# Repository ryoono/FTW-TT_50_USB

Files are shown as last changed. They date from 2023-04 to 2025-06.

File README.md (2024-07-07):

# FTW-TT_50_USB  

<span style="color: red; ">F</span>ake <span style="color: red; ">T</span>ype <span style="color: red; ">W</span>riter - <span style="color: red; ">T</span>etora <span style="color: red; ">T</span>ech lab _ <span style="color: red; ">5</span>.<span style="color: red; ">0</span>v _ <span style="color: red; ">USB</span> drive  
テトラ技研製 USB駆動 ニセタイプライター  

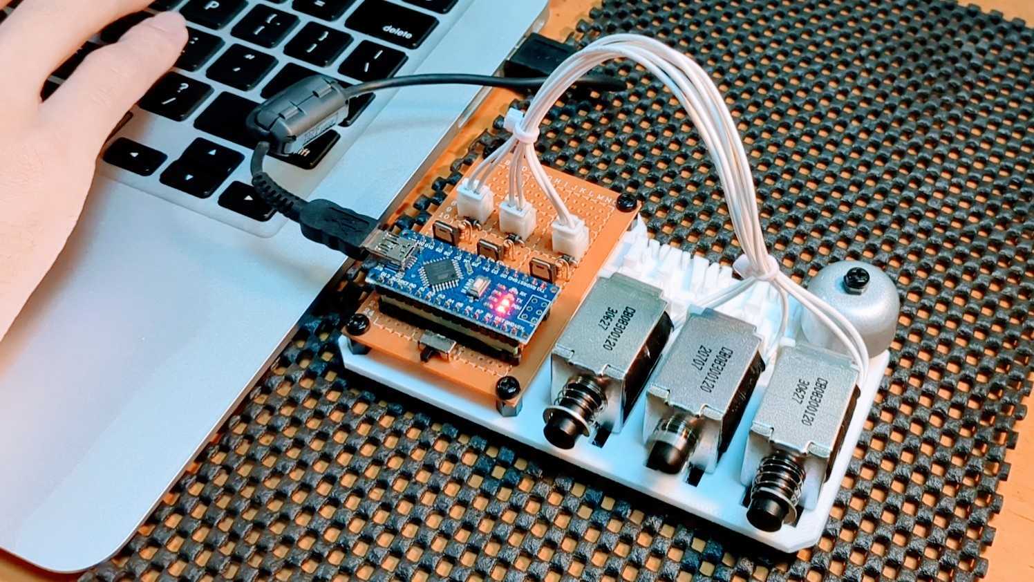
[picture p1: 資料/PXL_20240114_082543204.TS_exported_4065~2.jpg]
外観


**[紹介動画](https://youtu.be/UQrdH8_pX44?si=VVSs2FK_6RHxstvM)**

## 背景  
現代の消音キーボードに反抗すべく、タイプライターを叩いた時の音を楽しめるデバイスを作成する。  
タイプライター風キーボードも売ってはいるが、それを使っては味気ないので、外付けUSBデバイスとして実装する。  
当初、リレーで音を出そうと考えていたが、よくよく調べてみると二番煎じだった。  
そのため、急遽ソレノイドで音を出す仕様に変更した...   
[Silriumさん_USB KeyBoard RELAY](https://makezine.jp/blog/2015/08/mft2015_silrium.html)

## 概要  
キータイプ時にソレノイドを動作させ、タイプライターの音を表現する。  
音は2種類用意する。

| キー種類 | 音 | 備考 | 
| --- | --- | --- |
| 一般キー | メカニカル音 | エンターキー以外のキー | 
| エンターキー | ベル音 | |  

メカニカル音はソレノイドの動作音で再現する。  
ベル音はタイプライターの文字送り催促ベルを指しており、自転車のベルで再現する。  

## ハードウェア設計  
### 構成  
一般キー押下時の音を再現するために、ソレノイドを接続する。  
タイピングの間隔が80msを下回ると、ソレノイドのデッドタイムとかぶるため、一般キー用のソレノイドを2つ接続して対策する。  
エンターキー押下時の音は、ベルを鳴らすことで対応する。  
なお、エンターキーの押下間隔は80msを下回らないと仮定して、ソレノイドは1つのみ接続する。  
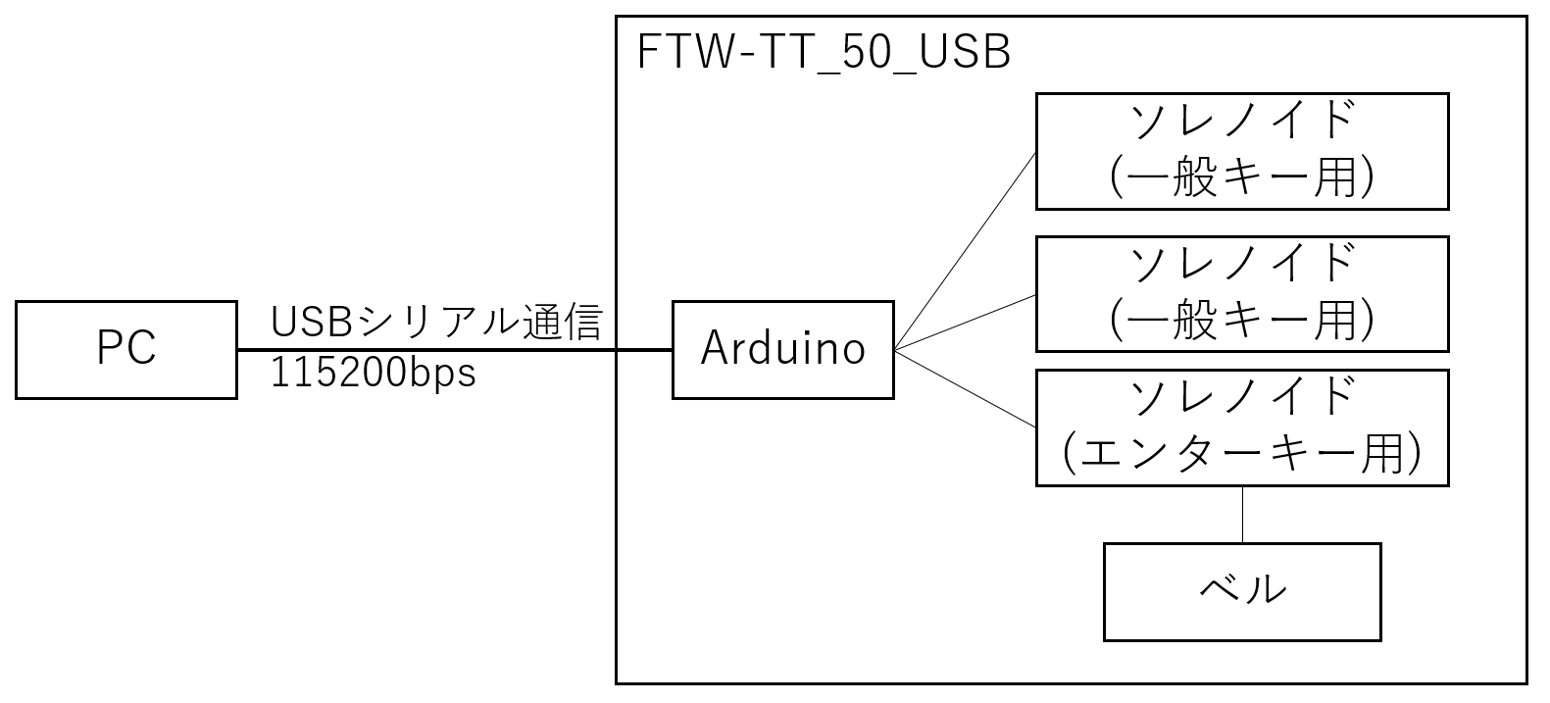
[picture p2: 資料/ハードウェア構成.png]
ハードウェア構成
 

### 回路図  
小型化を狙いpicマイコンで実装しようとしたが、時間が無いのでArduinoを使用する。  
Arduino Microを使用して設計したが、電源回りが弱いようで5Vピンから5V出力されないため、Nanoを使用する。  
使用するソレノイドには、ON/OFF 40[ms]ずつ計80[ms]のデッドタイムがあり、一般キー押下タイミングによっては、反応が追い付かない。  
そのため、ソレノイドを2個設置し、40[ms]のデッドタイムとすることで対応する。  
なお、2個以上のソレノイドを同時に動作させることはUSB2.0の規格上、電流が大きすぎるため同時動作ソレノイドは1つまでとする。  
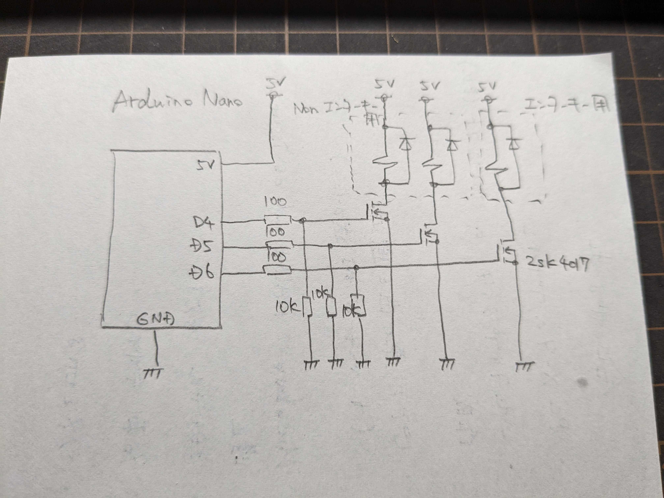
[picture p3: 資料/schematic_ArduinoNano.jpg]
schmatic
  

## ソフトウェア設計  
### PC側  
```mermaid
---
title: Fig. PC側処理_フローチャート
---

flowchart TD
    start1([開始])
    node0[Arduinoとの通信開始]
    node1[キーイベント監視開始]
    end1([終了])

    start2([キーイベント発生])
    node2[押下キー取得]
    switch1{押下キー}
    node3[Arduinoに'0'を送信]
    node4[Arduinoに'1'を送信]
    end2([終了])

    start1 --> node0
    node0 --> node1
    node1 --> end1

    start2 --> node2
    node2 --> switch1
    switch1 -- エンターキー --> node3
    switch1 -- エンターキー以外 --> node4
    node3 --> end2
    node4 --> end2
```

### デバイス側  
なぜ関数化しなかったのかが悔やまれるが、展示ギリギリだったので許してほしい。  

```mermaid
---
title: Fig. Arduino側処理_フローチャート
---

flowchart TD
    start1([開始])
    node0[シリアル受信チェック]
    switch0{受信有無}
    switch1{打鍵タイプ}
    switch2{受信キー}
    switch2_1{受信キー}
    node1[受信キーBuff = エンターキー]
    switch3{受信キーBuff}
    node2[受信キーBuff = 一般キー]
    node2_1[受信キーBuff = 一般キー]
    switch4{ソレノイド状態}
    end1([終了])

    start1 --> node0
    node0 --> switch0
    switch0 -- あり --> switch1
    switch1 -- 英語(1) --> switch2
    switch2 -- エンターキー('0') --> node1
    switch2 -- 一般キー('1') --> switch3
    switch3 -- なし(0) --> node2
    switch1 -- 日本語(0) --> switch2_1
    switch2_1 -- エンターキー('0') | 一般キー('1') --> node2_1
    node1 --> switch4
    node2 --> switch4
    switch2 -- それ以外--> switch4
    switch3 -- あり(!=0) --> switch4
    node2_1 --> switch4
    switch2_1 -- それ以外 --> switch4
    switch0 -- なし --> switch4

    switch10{受信キーBuff}
    node10[ソレノイドON時間設定 = 35ms]
    node11[ON中ソレノイドID = 3:エンターキー]
    node12[受信キーBuff初期化]

    node13[ソレノイドON時間設定 = 40ms]
    switch11{一般キーONソレノイド前回値}
    node14[ON中ソレノイドID = 1:一般キー]
    node14[ON中ソレノイドID = 2:一般キー]
    node15[受信キーBuff初期化]

    switch4 -- ON中(0以外) --> switch10
    switch10 -- エンターキー(1) --> node10
    node10 --> node11
    node11 --> node12
    switch10 -- 一般キー(0) --> node13
    node13 --> switch11
    switch11 -- 1 --> node14
    switch11 -- 2 --> node15

    switch20{ソレノイドON時間設定}
    switch21{ON中ソレノイドID}
    node20[ソレノイド1のみON]
    node21[ソレノイド2のみON]
    node22[ソレノイド3のみON]
    node23[ソレノイド全OFF]

    node30[1ms停止]

    node12 --> switch20
    node14 --> switch20
    node15 --> switch20
    switch20 -- 0以外 --> switch21
    switch21 -- 1:一般キー --> node20
    switch21 -- 2:一般キー --> node21
    switch21 -- 3:エンターキー --> node22
    switch20 -- 0 --> node23

    node20 --> node30
    node21 --> node30
    node22 --> node30
    node23 --> node30

    node30 --> end1
```

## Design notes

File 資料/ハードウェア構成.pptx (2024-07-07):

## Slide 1

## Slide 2

FTW-TT_50_USB

ソレノイド
(一般キー用)

ソレノイド
(一般キー用)

PC

USBシリアル通信
115200bps

Arduino

ソレノイド
(エンターキー用)

ベル

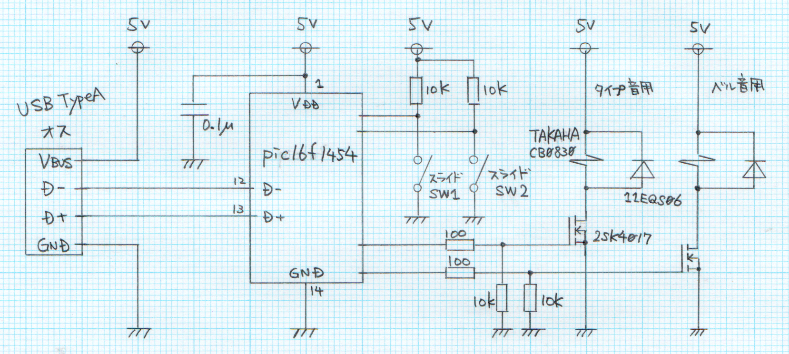
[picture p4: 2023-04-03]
資料/schematic.png

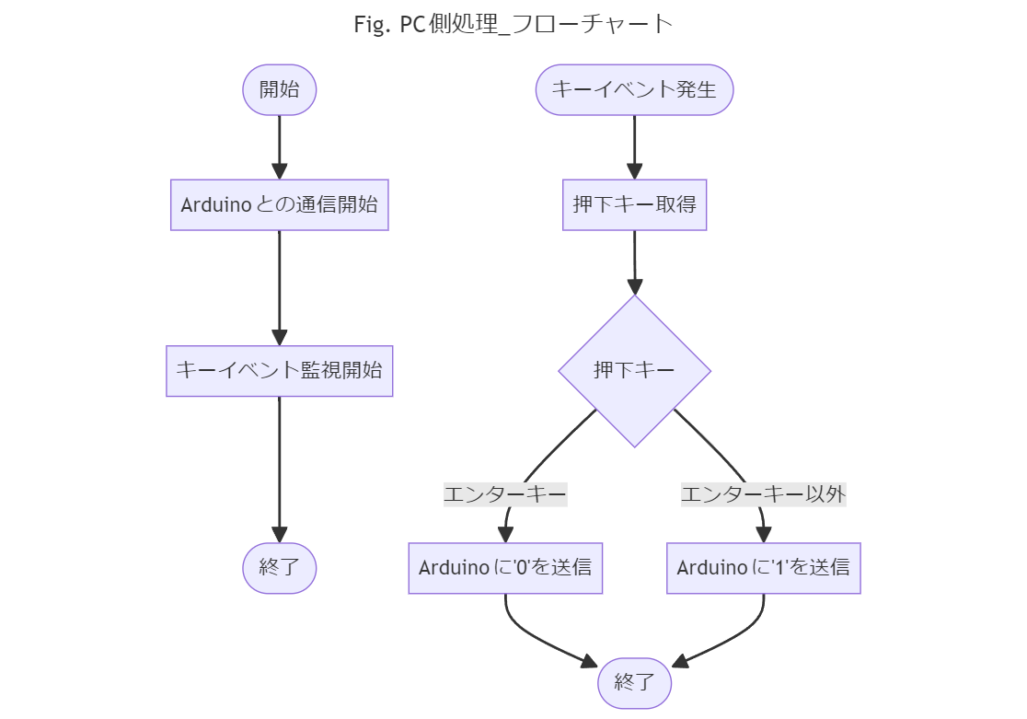
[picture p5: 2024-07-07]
資料/PC側フローチャート.png

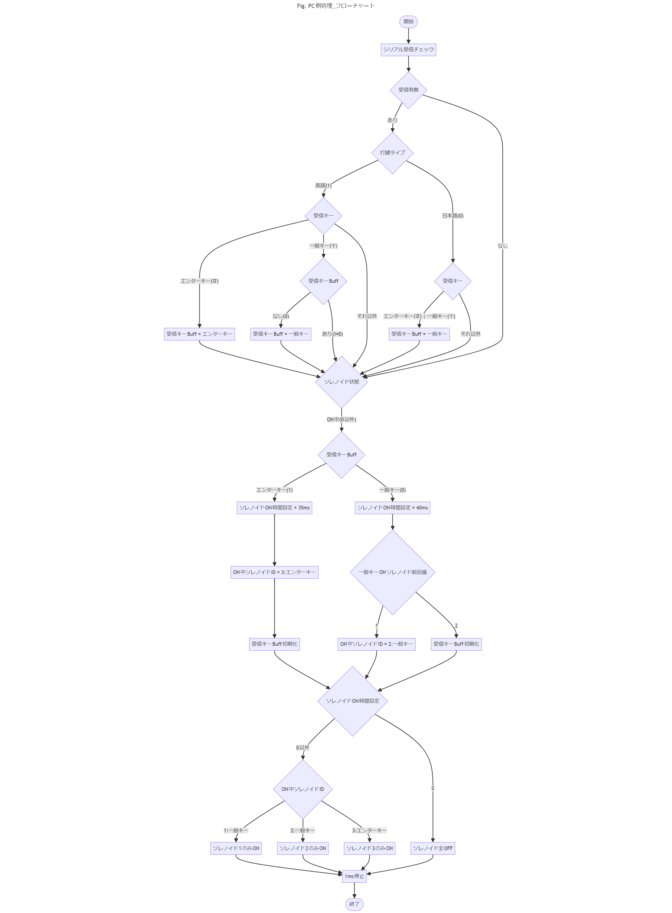
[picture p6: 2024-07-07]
資料/Arduino側フローチャート.png

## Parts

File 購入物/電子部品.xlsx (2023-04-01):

大項目 | 小項目 | 単価 | 個数 | 合計 | URL
マイコン | PIC16F1454 | 190 | 3 | 570 | https://akizukidenshi.com/catalog/g/gI-14680/
コネクタ | USBタイプA(オス) | 50 | 3 | 150 | https://akizukidenshi.com/catalog/g/gC-02236/
SW | スライドスイッチ １回路２接点 基板用 横向き | 25 | 6 | 150 | https://akizukidenshi.com/catalog/g/gP-15703/
ダイオード | ショットキーバリアダイオード ６０Ｖ１Ａ １１ＥＱＳ０６ （１０本入） | 160 | 1 | 160 | https://akizukidenshi.com/catalog/g/gI-08999/
FET | ＮｃｈパワーＭＯＳＦＥＴ ６０Ｖ５Ａ ２ＳＫ４０１７（Ｑ） | 30 | 5 | 150 | https://akizukidenshi.com/catalog/g/gI-07597/
ソケット | ＩＣソケット （１４Ｐ） （１０個入） | 100 | 1 | 100 | https://akizukidenshi.com/catalog/g/gP-00006/
基板 | 片面ガラスコンポジット・ユニバーサル基板 Ｂタイプ めっき仕上げ （９５×７２ｍｍ） 日本製 | 100 | 5 | 500 | https://akizukidenshi.com/catalog/g/gP-03230/
電解コンデンサ | 電解コンデンサー ４７μＦ１６Ｖ１０５℃ ルビコンＰＸ | 10 | 10 | 100 | https://akizukidenshi.com/catalog/g/gP-10270/
積層セラミックコンデンサ | 0.1uF | 100 | 1 | 100 | https://akizukidenshi.com/catalog/g/gP-13582/
 | 0.47uF | 110 | 1 | 110 | https://akizukidenshi.com/catalog/g/gP-15938/
抵抗 | 100Ω | 100 | 1 | 100 | https://akizukidenshi.com/catalog/g/gR-07803/
 | 15kΩ | 100 | 1 | 100 | https://akizukidenshi.com/catalog/g/gR-07840/
ソレノイド | CB0730 | 1220 | 2 | 2440 | https://www.takaha.co.jp/co/cb/
 | CB0830 | 1710 | 2 | 3420
 | CB1029 | 1830 | 2 | 3660

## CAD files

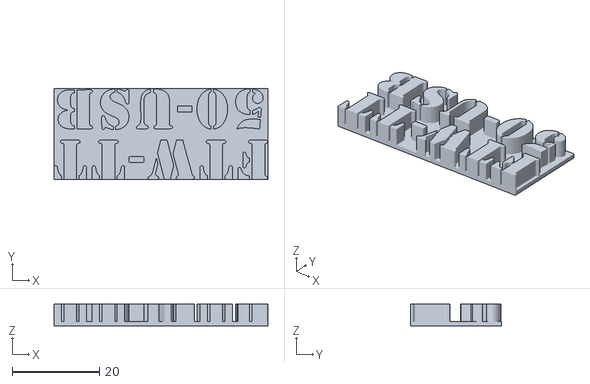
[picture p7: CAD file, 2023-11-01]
3D_Data/文字プレート.stl
49.1 x 20.8 x 5.00

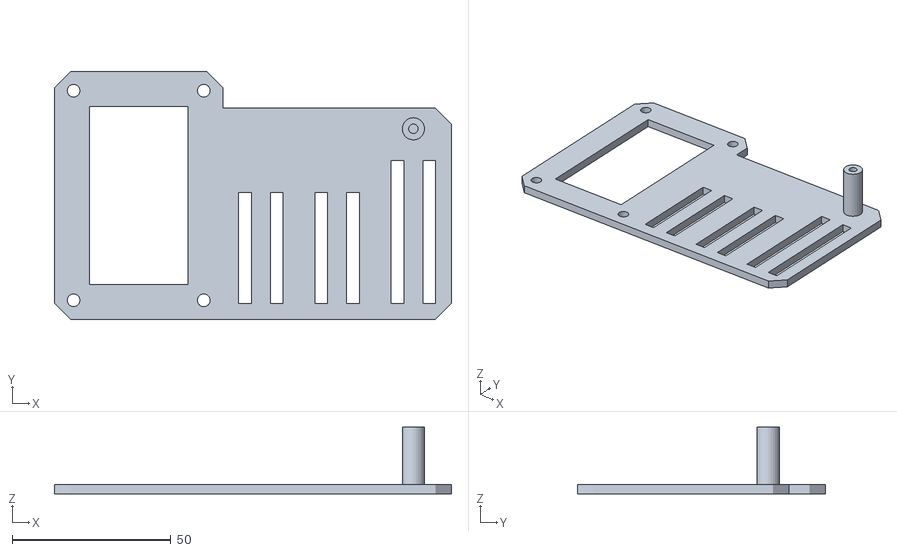
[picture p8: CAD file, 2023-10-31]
3D_Data/固定台.stl
125.0 x 78.0 x 21.0

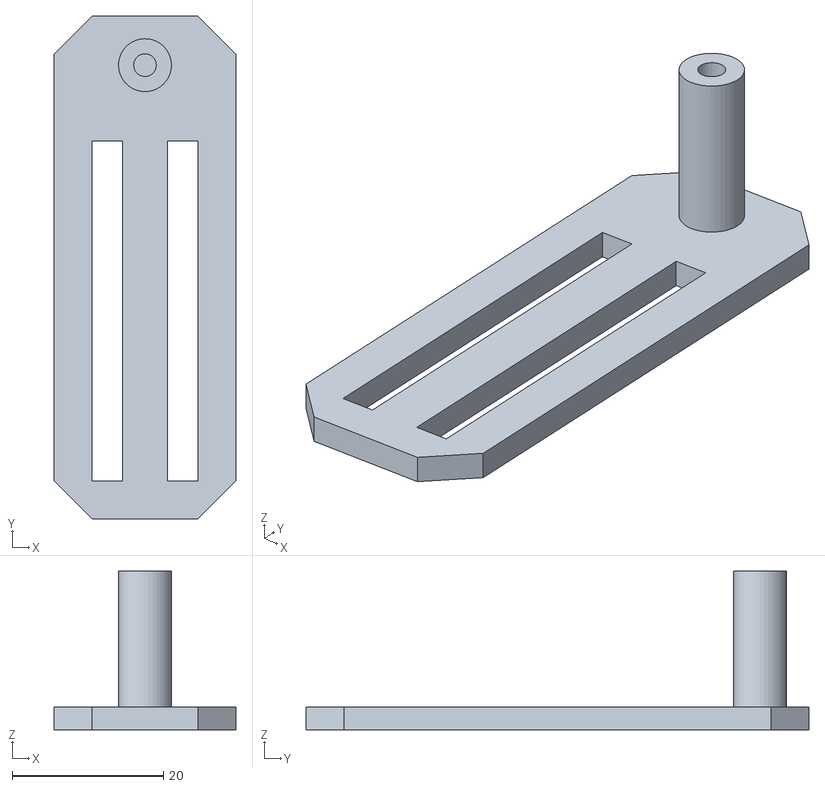
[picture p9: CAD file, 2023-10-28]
3D_Data/ベル動作確認用土台.stl
24.0 x 66.5 x 21.0

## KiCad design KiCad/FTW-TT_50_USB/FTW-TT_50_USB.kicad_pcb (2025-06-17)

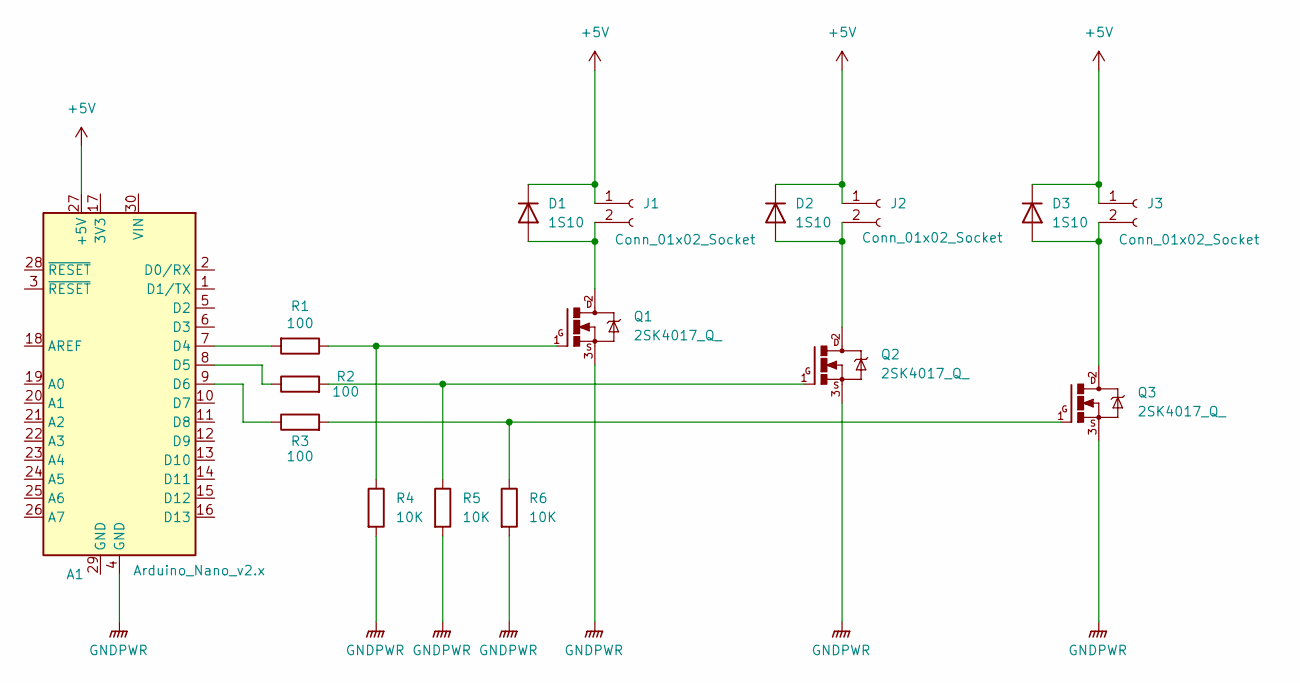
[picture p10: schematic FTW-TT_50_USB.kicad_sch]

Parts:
A1: Arduino_Nano_v2.x; Arduino_Nano
D1, D2, D3: 1S10; D_DO-41_SOD81_P7.62mm_Horizontal
J1, J2, J3: Conn_01x02_Socket; JST_XH_B2B-XH-AM_1x02_P2.50mm_Vertical
Q1, Q2, Q3: 2SK4017_Q_; TO230P230X650X740-3P
R1, R2, R3: 100; R_Axial_DIN0207_L6.3mm_D2.5mm_P10.16mm_Horizontal
R4, R5, R6: 10K; R_Axial_DIN0207_L6.3mm_D2.5mm_P10.16mm_Horizontal

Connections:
+5V: A1.27 (+5V), D1.1 (K), D2.1 (K), D3.1 (K), J1.1, J2.1, J3.1
GNDPWR: A1.4 (GND), Q1.3, Q2.3, Q3.3, R4.2, R5.2, R6.2
unnamed: A1.7 (D4), R1.2
unnamed: A1.8 (D5), R2.1
unnamed: A1.9 (D6), R3.1
unnamed: D1.2 (A), J1.2, Q1.2
unnamed: D2.2 (A), J2.2, Q2.2
unnamed: D3.2 (A), J3.2, Q3.2
unnamed: Q1.1, R1.1, R4.1
unnamed: Q2.1, R2.2, R5.1
unnamed: Q3.1, R3.2, R6.1

Board: 2 copper layers, 16 parts (0 on the bottom side), 11 nets, no tracks yet.

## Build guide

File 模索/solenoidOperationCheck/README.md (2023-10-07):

# solenoidOperationCheck    

ソレノイドの最適なON/OFF時間を模索するためのS/Wを作成する．  
ソレノイドON/OFF時間が短すぎると，ソレノイドが反応する前に処理が完了してしまうため，最適な時間を求める意図がある．  

## 仕様  
シリアル通信でソレノイドON/OFF時間を指定する．  

### コマンド一覧  

|コマンド|結果|
|:---|:---|
|on [数字]|ソレノイドのON時間を指定する(ms)|
|off [数字]|ソレノイドのOFF時間を指定する(ms)|
|continue|連続稼働|
|single|単発稼働|
|start|開始|
|s|停止|

## 回路図
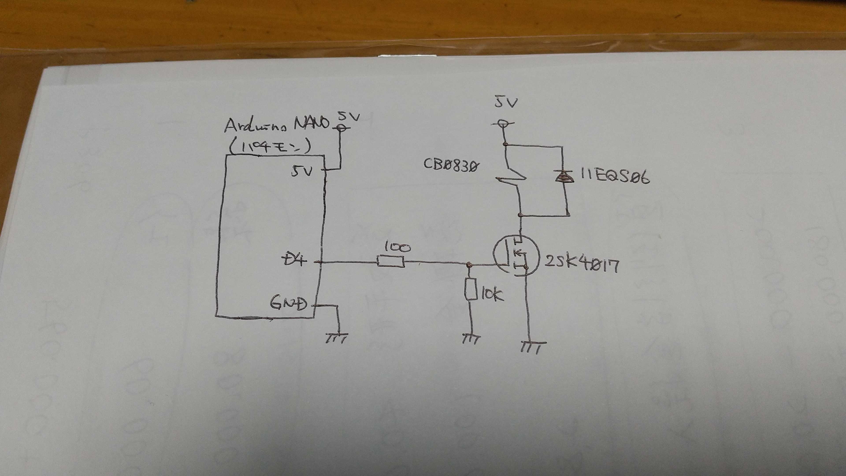
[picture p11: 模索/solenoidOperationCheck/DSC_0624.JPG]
回路図


## 結果  
ON/OFF時間ともに，40[ms]が最小時間となった． 
動作動画↓   
[Twitter動画埋め込めないので，リンク貼っときます](https://twitter.com/TetoraTechLab/status/1645044216073191426)

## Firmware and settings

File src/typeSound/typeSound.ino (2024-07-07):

#define KEY_NULL      '-'
#define ENTER_KEY     '0'
#define NON_ENTER_KEY '1'

#define SOL_PIN_1     5
#define SOL_PIN_2     6
#define SOL_BELL_PIN  4
#define SW_PIN        A4
#define LED_PIN       13

#define SOL_ON_TIME         40  // ソレノイドのON時間(一般キー)[msec]
#define SOL_ENTER_ON_TIME   35  // ソレノイドのON時間(エンターキー)[msec]
#define SOL_OFF_TIME        40  // ソレノイドのOFF時間[msec]

#define SW_EN HIGH  // スイッチ状態_英語
#define SW_JP  LOW  // スイッチ状態_日本

bool ledState;
int  swState; // SWの状態

// 0:OFF, 1:SOL_PIN_1 ON, 2:SOL_PIN_2 ON, 3:SOL_BELL_PIN ON
unsigned char solOnState;
unsigned char solPinCnt;      // 一般キー用ソレノイド動作回数
int solOnRestTime;            // ソレノイドON時間計測用タイマ
// 0:無し, 1:エンターキー, 2:一般キー
unsigned char solOnBuff;

void setup() {

  solOnState = 0;
  solPinCnt = 0;
  solOnRestTime = 0;
  solOnBuff = 0;
  
  pinMode(    SOL_PIN_1, OUTPUT);
  pinMode(    SOL_PIN_2, OUTPUT);
  pinMode( SOL_BELL_PIN, OUTPUT);
  pinMode(      LED_PIN, OUTPUT);
  pinMode(            1,  INPUT); // Vccが当たりそうだから入力ピンにしておく
  pinMode(       SW_PIN, INPUT_PULLUP);

  digitalWrite(    SOL_PIN_1, LOW);
  digitalWrite(    SOL_PIN_2, LOW);
  digitalWrite( SOL_BELL_PIN, LOW);
  digitalWrite(      LED_PIN, LOW);
  
  ledState = true;
  swState = digitalRead( SW_PIN );

  Serial.begin( 115200 );
}

void loop() { 

  swState = digitalRead( SW_PIN );
  
  // シリアル受信した場合
  while( Serial.available() > 0 ){
    char buff;
    buff = Serial.read();

    Serial.println( buff );

    if( swState == SW_EN ){
      // エンターキーを優先する
      if( buff == ENTER_KEY ){
        solOnBuff = 1;
      }
      // 一般キー
      else if( (buff == NON_ENTER_KEY) && (solOnBuff == 0) ){
        solOnBuff = 2;
      }
    }
    else{
      // 一般キー
      if( (buff == ENTER_KEY) || (buff == NON_ENTER_KEY) ){
        solOnBuff = 2;
      }
    }
  }

  // 全部のソレノイドが解放されている場合に実行
  if( !solOnState ){
    // エンターキーをセット
    // エンターキーを連続で叩くことは無いと想定しているため，
    // 連続で叩かれると最初の1回しかベルが鳴らない
    if( solOnBuff == 1 ){
      solOnRestTime = SOL_ENTER_ON_TIME;
      solOnState = 3;
      solOnBuff = 0;
      ledState = !ledState;
    }
    // 一般キーをセット
    // 40msecのOFFタイムを減らすために，2つのソレノイドを交互に動作させている
    else if( solOnBuff == 2 ){
      solOnRestTime = SOL_ON_TIME;
      solOnState = (solPinCnt++ % 2) + 1;
      solOnBuff = 0;
      ledState = !ledState;
    }
  }

  if( solOnRestTime != 0 ){
    if( solOnState == 1 ){
      digitalWrite(    SOL_PIN_2,  LOW);
      digitalWrite( SOL_BELL_PIN,  LOW);
      digitalWrite(    SOL_PIN_1, HIGH);
    }
    else if( solOnState == 2 ){
      digitalWrite(    SOL_PIN_1,  LOW);
      digitalWrite( SOL_BELL_PIN,  LOW);
      digitalWrite(    SOL_PIN_2, HIGH);
    }
    else if( solOnState == 3 ){
      digitalWrite(    SOL_PIN_1,  LOW);
      digitalWrite(    SOL_PIN_2,  LOW);
      digitalWrite( SOL_BELL_PIN, HIGH);
    }

    // カウンタの更新
    if( !(--solOnRestTime) ){
      solOnState = 0;
    }
  }
  else{
    digitalWrite(    SOL_PIN_1, LOW);
    digitalWrite(    SOL_PIN_2, LOW);
    digitalWrite( SOL_BELL_PIN, LOW);
  }

  // LED点灯(ソレノイド動作ごとに点滅)
  if( ledState ) digitalWrite( LED_PIN, HIGH);
  else          digitalWrite( LED_PIN,  LOW);
  
  // 1msecごとに実行する
  delay( 1 );
}

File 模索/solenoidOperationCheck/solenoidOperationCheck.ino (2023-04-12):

#define MOVE_SINGLE   0 // 単発稼働
#define MOVE_CONTINUE 1 // 連続稼働

#define SOL_PIN 4 // ソレノイド制御用ピン番号

bool startFlag; // 稼働状態 false:停止 / true:起動
char startType; // 稼働タイプ
int  onTime;    // ソレノイドのON時間[ms]
int  offTime;   // ソレノイドのOFF時間[ms]

void setup() {

  startFlag = false;        // 停止に指定
  startType = MOVE_SINGLE;  // 単発に指定

  onTime  = 1000; // 初期値は1000[ms]
  offTime = 1000;

  pinMode( SOL_PIN, OUTPUT);
  digitalWrite( SOL_PIN, LOW);

  Serial.begin( 9600 );
  Serial.println("コマンド詳細はREADME.mdを参照してください");
  Serial.println("例外処理など入れてないため，コマンドを間違えないように注意してください");
}

void loop() {

  // 何らかのデータを受信した場合の処理
  if ( Serial.available() > 0 ) {
    // 終端文字によってここは変更．
    // macだとCR+LFのため，CRまでで切る
    String command = Serial.readStringUntil('\r');

    // ##################################
    // ####---- コマンド受信時の処理 ----####
    
    // ソレノイドのON時間を指定するコマンド受信時
    if( command.indexOf("on ") == 0 ){
      String onTime_s = command.substring( 3, command.length());
      onTime = onTime_s.toInt();
    }
    // ソレノイドのOFF時間を指定するコマンド受信時
    else if( command.indexOf("off ") == 0 ){
      String offTime_s = command.substring( 4, command.length());
      offTime = offTime_s.toInt();
    }
    // 連続稼働コマンド受信時
    else if( command.compareTo("continue") == 0 ){
      startType = MOVE_CONTINUE;
    }
    // 単発稼働コマンド受信時
    else if( command.compareTo("single") == 0 ){
      startType = MOVE_SINGLE;
    }
    // 開始コマンド受信時
    else if( command.compareTo("start") == 0 ){
      startFlag = true;
    }
    // 停止コマンド受信時
    else if( command.compareTo("s") == 0 ){
      startFlag = false;
    }
  }

  // #################################
  // ####---- ソレノイド稼働処理 ----####
  
  // startFlagがtrueならばソレノイドを稼働する
  // startTypeが単発稼働ならばstartFlagをfalseにする
  if( startFlag == true ){
    
    digitalWrite( SOL_PIN, HIGH);
    delay(onTime);
    digitalWrite( SOL_PIN, LOW);
    delay(offTime); 
    
    if( startType != MOVE_CONTINUE ){
      startFlag = false;
    }
  }
}

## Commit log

2023-03-30 パーツリスト更新
    [電子部品.xlsx]
2023-04-02 Delete ~$電子部品.xlsx
    一時ファイル削除
2023-04-03 回路図追加
2023-04-04 雛形作成
2023-04-05 概要追記
2023-04-06 回路図追記
2023-04-07 模索用ディレクトリ追加
2023-04-07 メモを追加
2023-04-07 ソレノイド動作チェックS/W雛形追加
2023-04-08 模索の取説書き始め
2023-04-09 取説追加
2023-04-09 コマンド受け取る処理実装
2023-04-09 ソレノイド稼働処理実装
2023-04-11 結果記載
2023-04-12 動かなかった箇所の修正
2023-04-13 少し追記(特に変更無し)
2023-04-16 名称追加
2023-10-07 回路図反映
2023-10-07 背景追記
2023-10-15 デバイス側プロジェクトファイル作成
2023-10-15 既存のサンプルコード使うことにした
2023-10-15 サンプルコード_コンパイル確認
2023-10-15 出典記載、メモ追加
2023-10-15 文字コードをutf-8に変更
2023-10-23 バックグラウンドキー取得模索格納
2023-10-23 コメント追加
2023-10-23 バックグラウンドキー取得&Arduinoと通信するコード追加(動作未確認)
2023-10-24 動作確認済み(エンター以外)
2023-10-24 メモ追加
2023-10-24 設計変更反映(デバイス側ICの変更)
2023-10-25 通信速度修正 & ソレノイド2個に対応改修
2023-10-26 エンターキー押下時の不具合修正
2023-10-28 ベル動作確認用土台追加
    [ベル動作確認用土台.stl]
2023-10-31 固定台追加
    [固定台.stl]
2023-10-31 コード調整
2023-11-01 EN/JPモード追加
2023-11-01 プレート追加
    [文字プレート.stl]
2023-11-01 picのプロジェクトフォルダを削除
2023-11-18 NT名古屋最終
2024-01-14 誤記修正
2024-07-07 紹介動画の追加 & 句読点の統一(，→、)
2024-07-07 PC側処理のフローチャート追加
2024-07-07 PC側ふとーチャート画像追加
2024-07-07 不必要な処理削除 & コメント修正
2024-07-07 Arduino側フローチャート追加
2024-07-07 画像サイズ修正
2024-07-07 ハードウェア構成追加
2024-07-07 外観画像追加
2025-06-17 KiCadファイル追加
    [FTW-TT_50_USB.kicad_pcb, FTW-TT_50_USB.kicad_sch]
